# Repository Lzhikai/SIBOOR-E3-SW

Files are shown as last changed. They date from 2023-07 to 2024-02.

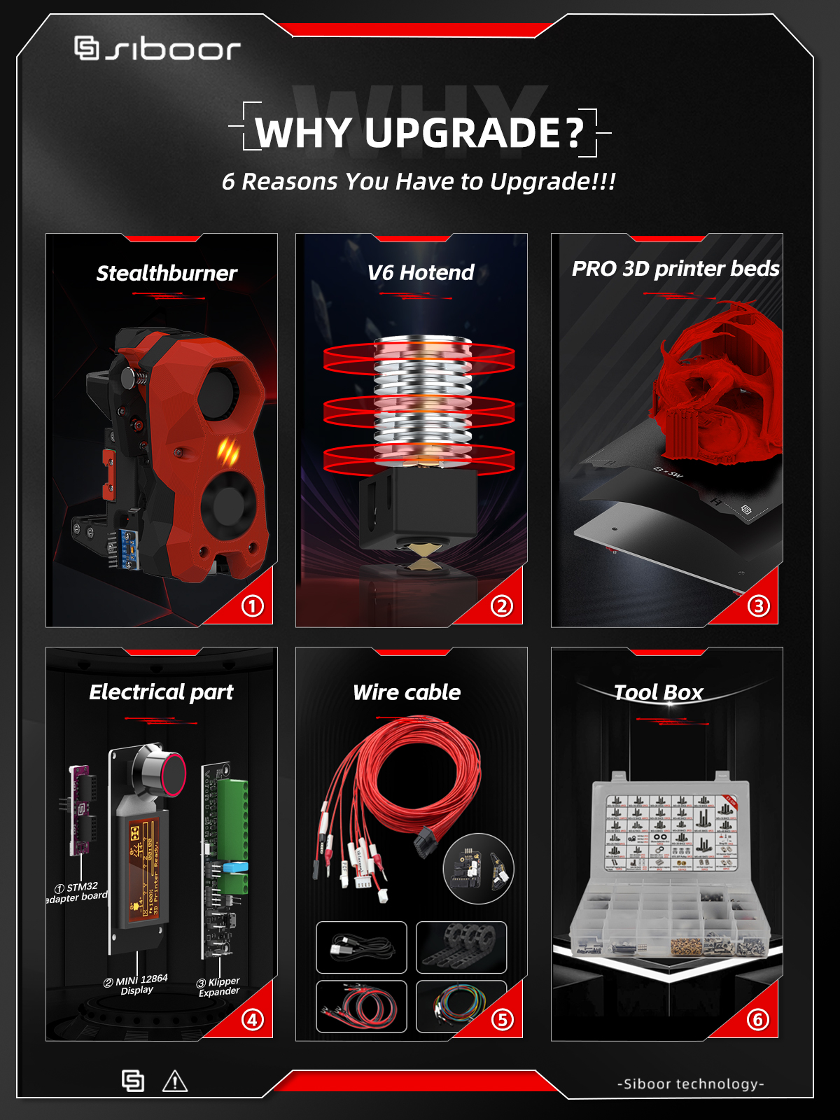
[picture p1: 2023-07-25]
Images/1 (10).jpg

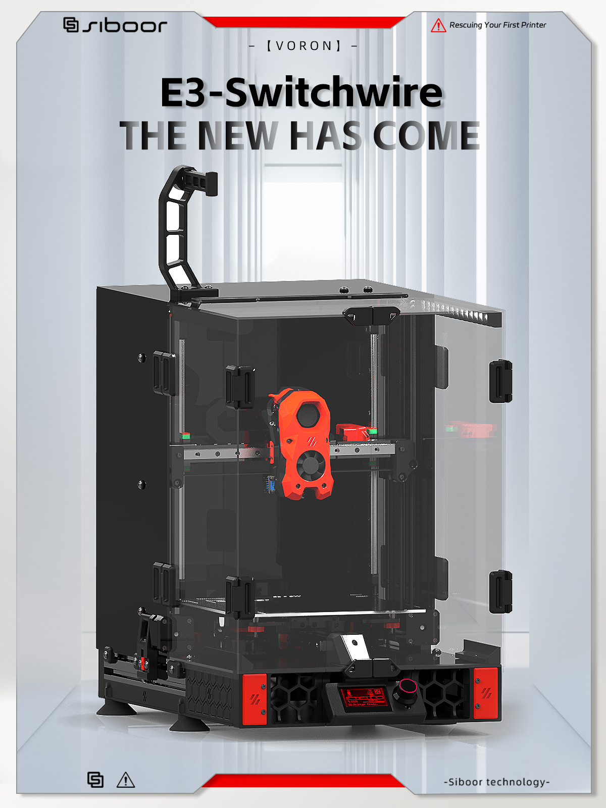
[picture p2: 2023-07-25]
Images/1 (7).jpg

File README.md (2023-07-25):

#SIBOOR E3-SW
We are pleased to announce that we at SIBOOR have launched a conversion kit for E3-SW.
It is based on the open source project DaRk_dOg.

The modifications are as follows
- Use a more cost-effective door closer instead of the KEY-BAK S48K
- Fixed the STL file of Y limit switch
- Used 24→5V step-down module instead of 5V power supply.
- Added klipper extender
- Added STM32 adapter board

Currently the instructions and videos are being made in a hurry, please assemble according to the CAD file, if you encounter problems, you can demand help in discord.

-----------------------------------------------------------------------------------------------------------------------------------------------
Original open source link：https://github.com/boubounokefalos/Ender_SW
architect (of a project)：DaRk_dOg

Original content (citation)

# Ender 3 Pro/V2 to Switchwire Conversion Release.2

This is a full conversion of the popular Ender 3 Pro/V2 to a Voron Switchwire. The motivation came from [Triano](https://github.com/walttriano) and [his awesome original conversion](https://github.com/walttriano/VoronUsers/tree/master/printer_mods/Triano/Ender_3Pro_Switchwire) that served as a starting point, however everything was re-designed from scratch (in order to follow the Voron guidelines and aesthetics more accurately). Another factor that led to this re-design, was the need to be able to enclose this printer in a, visually, pleasant and, structurally, functional way. The ingenious design of 5x MGN12H Linear Rails - 300mm (dual Y axis rail) from Triano was preserved and the printing volume is ~220x220x220.

# Release 2 Update Changelog:

- CAD files cleaned up.
- Small corrections to parts.
- Added printable deck files (still it's recommended to laser cut them though)
- Added different .dxfs for rear black panels (in case anyone wants to cut the panels from a material that is not same on both surfaces)
- Added the option to use the stock Ender 3 LCD screen.

# Rev.2 Update Changelog:

- Every change happened in order to improve the build process and the design overall.
- All screw sizes and types are properly documented in the CAD (soon there will be a conversion BOM also). Also no more “exotic” sizes, everything is according to what VORON is using officially.
- Current conversion’s enclosure is 100% compatible with the new update (except of the deck panels ofc).
- XZ Blocks improved fit for the X v-slots and are also modified to use 30mm BHCS (like the original SW).
- Y Axis, new front idler (in order to achieve a mounting point for the front grill), improved clearance for the rear Y motor mount. All use BHCS screws now.
- Split bed carriage with size and clearance corrections. Made uppon the design recommendation of Steve. Also Y belt clips have a bit more clearance on the upper side, in order to leave some space for spare belt 🙂
- XZ motors have thinner XZ tensioners to avoid the lower “split” (kudos to Steve for that ALSO).
- We are now using the original SW Spool Holder (for easier installation, due to clearance)
- Front Grills have now the LCD mount of the original SW. They also mount to the extended sides just by M3 screws.
- Rear Grills mount by M5x16 BHCS screws now. Also the inlet has moved to the side (in order to have a straight and easier connection with the PSU), this was also a recommendation by Steve and he was more than kind to share his original .F3D file. Both stock Ender and C14 inlets are compatible.
- Removed material from the grills, in order to save some plastic and cut down print time.
- PSU is now mounted parallel to the side extrusions and RS25 can be mounted in the front of the printer.
- Redesigned mounts for the Board and RPi (no more shelf and moooahr clearance!)

And last but not least…
-The side extensions. Front and rear side extensions are designed to extend the frame for aesthetical and a few practical reasons (clearance and NO MORE NOTCH). They are sturdy enough but keep in mind that you will not move around the printer by lifting it from there.

## Info

Various parts _can*_ be recycled from the Ender 3 Pro/V2, most important ones are:
- The frame (though a 310mm extrusion is needed for the X. You can chop the original one to length).
- The MeanWell PSU.
- The heatbed assemble.
- The original board.
- XYZ motors (as long as you can pull off the pulleys. An aftermarket 20mm motor is needed for the printhead extruder though).
- All the cables that don't go through the cable-chains (for there, silicone or PTFE cable is adviced).
- 4010 fan for the tool cooling.

*cheaping out in parts can lead into several problems, such as poor printing quality or, even worse, safety hazard. Keep that in mind and use parts from the official Switchwire BOM.

## Files

- Most of the printed part files needed for this conversion, are included in this git (you will only need to get the Stealthburner print files from the [official Switchwire git](https://github.com/VoronDesign/Voron-Stealthburner) ).
- CAD files (.f3d and .STEP) are provided, in order to help the building process, but they also serve as a BOM (in case you need to find proper screw lengths etc).
- DXF files in order to cut your enclosure panels.
- BOM (Sometime...)

## Credits

- Ofc to Triano, as his design served as base.
- To Steve (THE Steve!) for pointing out weak parts, that had to be redesigned, his tips and files and being a helpful person in general.
- To sdukan#9213 for his valuable help into troubleshooting the Ender 3 V2 differences, electronics (and in general).
- To all of this awesome community of people and especially the [ender_conversion_chat](https://discord.com/channels/460117602945990666/947303252372906014).
- To Voron design team for all the valuable resources and the solid base.

## Disclaimer

This is a very carefuly designed build.. however mistakes could have been made. By deciding to build this conversion, you are responsible for any possible damage done to the printer or even yourself.

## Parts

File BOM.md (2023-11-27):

| style | Name | Quantities | Specs |
|---|---|---|---|
| "Fasteners | M3×8 SHCS | 134 | Black Nickel Plated  |
| | M3×10 SHCS | 4 | Black Nickel Plated  |
| | M3×12 SHCS | 46 | Black Nickel Plated  |
| | M3×16 SHCS | 12 | Black Nickel Plated  |
| | M3×20 SHCS | 10 | Black Nickel Plated  |
| | M3×25 SHCS | 8 | Black Nickel Plated  |
| | M3×30 SHCS | 15 | Black Nickel Plated  |
| | M3×40 SHCS | 15 | Black Nickel Plated  |
| | M3×50 SHCS | 4 | Black Nickel Plated  |
| | M5×40 SHCS | 12 | Black Nickel Plated  |
| | M4×6 SHCS | 2 | Black Nickel Plated  |
| | M4×20 SHCS | 3 | Black Nickel Plated  |
| | M5×10 BHCS | 40 | Black Nickel Plated  |
| | M5×16 BHCS | 35 | Black Nickel Plated  |
| | M5×20 BHCS | 2 | Black Nickel Plated  |
| | M5×25 BHCS | 8 | Black Nickel Plated  |
| | M5×30 BHCS | 10 | Black Nickel Plated  |
| | M5×40 BHCS | 8 | Black Nickel Plated  |
| | M5×25 FHCS | 4 | Black Nickel Plated  |
| | M5 Post-install T-nut | 35 | / |
| | M5 Hammer Head T-nuts | 30 | / |
| | M3 Hammer Head T-nuts | 65 | / |
| | M3 Nut | 6 | Black Nickel Plated  |
| | M4 Nut | 4 | Black Nickel Plated  |
| | M5 Nut | 9 | Black Nickel Plated  |
| | M4×30 FHCS | 4 | Black Nickel Plated  |
| | M3 Brass heatstake inserts - short M3x5x4 | 120 | / |
| | M3Shim 3×7×0.5 | 2 | Black Nickel Plated  |
| | M5 1mm Shim  5×10×1 | 24 | Black Nickel Plated  |
| | M5 rubber gasket 5×10×1 | 12 | / |
| | M2x10 Self Tapping Screws for Plastic | 12 | Black Nickel Plated  |
| | M3×6 FHCS | 24 | Black Nickel Plated  |
| | M3×6 BHCS | 10 | Black Nickel Plated  |
| | M5×45 BHCS | 4 | Black Nickel Plated  |
| | 6mm x 3mm Round Neodymium Magnets | 8 | / |
| | Aluminum column φ5×8×8 | 4 | / |
| "Frame | 2020 Extrusion 310mm long | 1 | / |
| "Electronics  | Nema17 17HS16-2004S1 | 2 | SIBOOR |
| | 24V to 5V DC Voltage Reducer | 1 | / |
| | NEMA14 36mm pancake Motor with 10 tooth gear | 1 | OMC |
| | 5015 blower fans 24V | 1 | SIBOOR |
| | 4010 axial fan 24V | 1 | SIBOOR |
| | 6020 axial fan 24V | 1 | SIBOOR |
| | IEC320 C14 inlet | 1 | / |
| | Stealthburner Neopixel RGBW leds | 1 | SIBOOR |
| | Omron TL-Q5MC2-Z | 1 | OMRON |
| | ADXL345 PCB | 1 | / |
| | ADXL345 lineup | 1 | SIBOOR |
| | V6 hotend | 1 | SIBOOR |
| | 24V 65W Heating（6×15mm Wire length 15cm） | 1 | SIBOOR |
| | NTC 3950 100K（3×15mm Wire length 15cm） | 1 | SIBOOR |
| | klipper expansion board | | FYS |
| | MINI 12864 display | 1 | FYS |
| | STM32 for MINI 12864 Display Converters | 1 | FYS |
| | TYPE-C cable 0.75 meters | 1 | / |
| | Android Data Cable 0.5m | 2 | / |
| | LED strip light 24V white 100mm wire | 1 | / |
| | Micro Switch（15CM） | 1 | SIBOOR |
| Cable Section | Toolhead PCB 14PIN+2PIN Teflon wire | 1 | SIBOOR |
| | raspberry Power supply line | 1 | / |
| | Toolhead PCB（Stealthburner CW2 2PCS） | 1 | SIBOOR |
| | High Flex Wire 20gauge | 2 | / |
| | High Flex Wire 20gauge | 2 | / |
| | Nylon Cable Ties (1.8mm wide or smaller) | 50 | / |
| "Motion | MGN12H 300mm linear guide | 5 | SIBOOR |
| | GT2 20T Pulley (5mm ID 6mm W) | 3 | / |
| | F695 Bearing | 20 | NSK |
| | GT2 Open Belt LL-2GT-6 (6mm wide) - 1500mm | 1 | Gates |
| "Buildplate | 235×235 Black PEI | 1 | / |
| "Panels | Deck left | 1 | / |
| | Deck right | 1 | / |
| | Deck under | 1 | / |
| | Rear Panel | 1 | / |
| | Side Rear panel | 2 | / |
| | Top Rear Panel | 1 | / |
| | Side Clear Panel | 2 | / |
| | Door | 2 | / |
| | Top Clear Panel | 1 | / |
| | Black Door Closer (1KG) | 1 | / |
| "Misc. | Rubber Compressor Foot | 4 | / |
| | 3M 5952 VHB tape 2CM×3M | 1 | 3M |
| | Openable drag chain 10×10 | 3 | / |
| "Extruder | BMG Extruder Kit（With red POM gears） | 1 | SIBOOR |

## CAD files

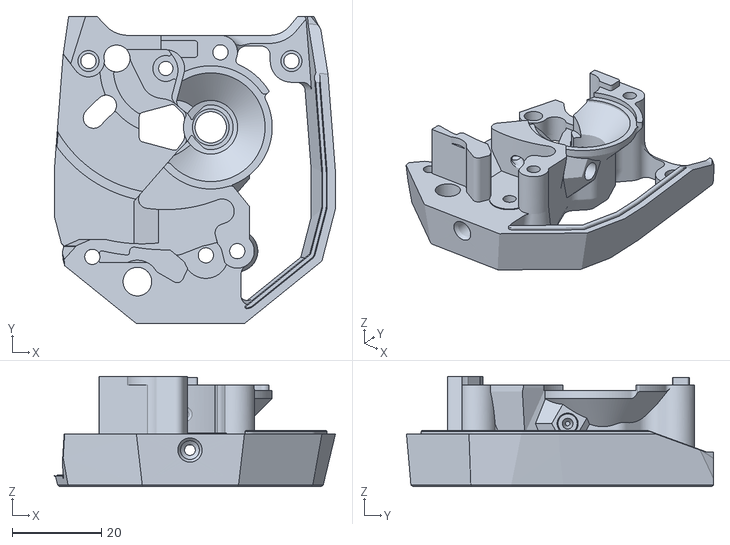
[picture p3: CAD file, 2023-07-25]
STLS - SIBOOR/Hotend/main_body.stl
62.8 x 68.7 x 24.7

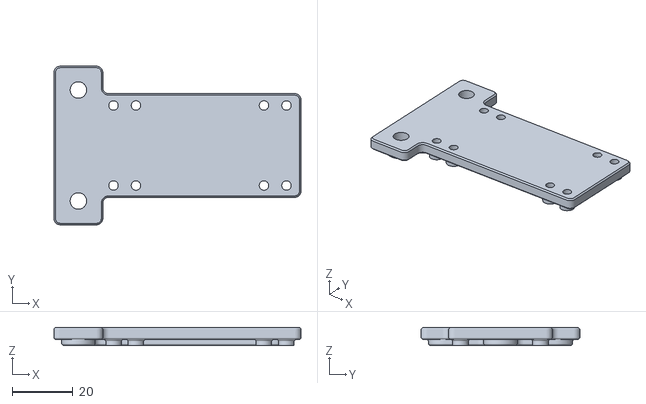
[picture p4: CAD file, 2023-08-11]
STLS - SIBOOR/Electronics/24 Buck 5V module fixing bracket（SIBOOR）.stl
81.0 x 52.0 x 6.00

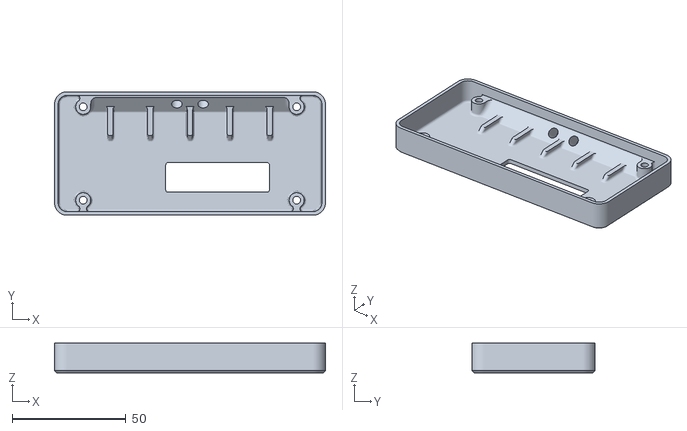
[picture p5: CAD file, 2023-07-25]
STLS - SIBOOR/Electronics/Mini12864/lcd_case_rear_mini12864.stl
119.0 x 54.2 x 13.0

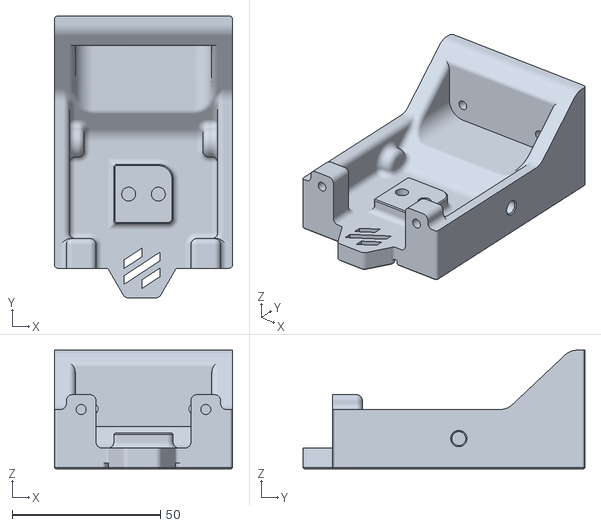
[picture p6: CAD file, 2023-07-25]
STLS - SIBOOR/Extentions/front_extention_left_a.stl
60.0 x 95.0 x 40.0

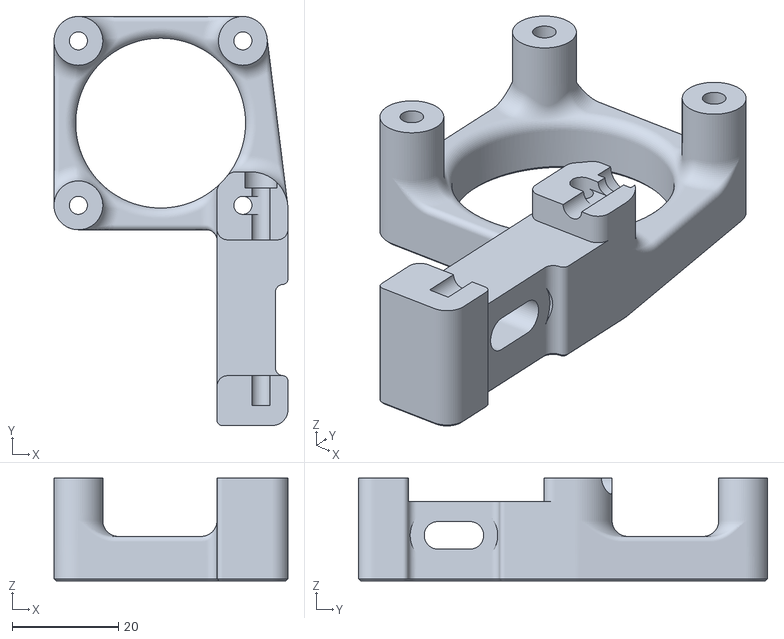
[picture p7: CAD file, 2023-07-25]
STLS - SIBOOR/Gantry/XZ Axis/z_motor_mount_b.stl
44.1 x 77.1 x 19.4

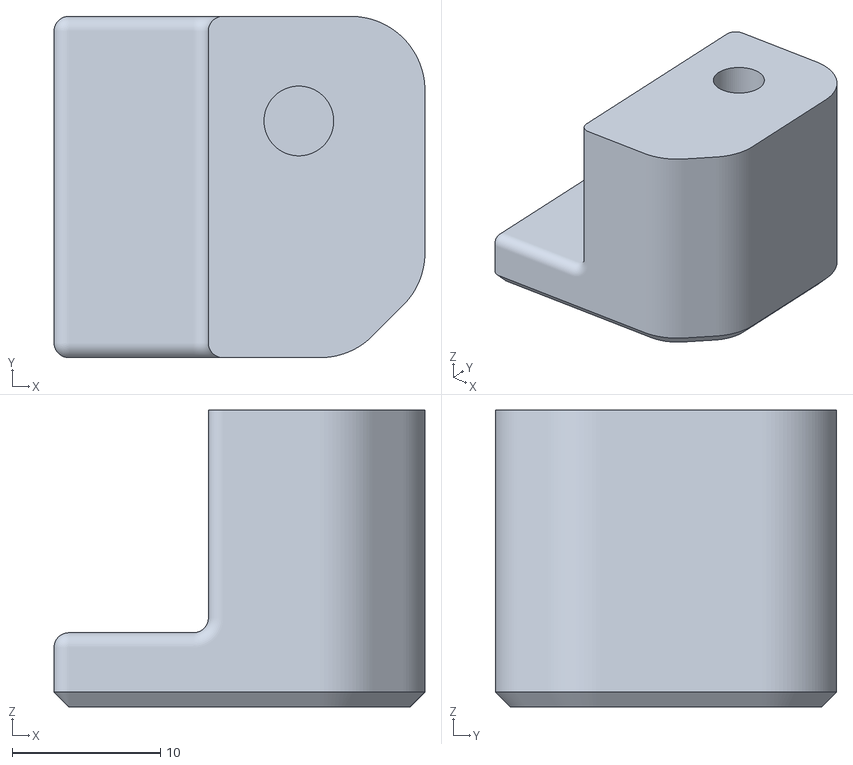
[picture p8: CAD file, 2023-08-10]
STLS - SIBOOR/Grills/grill_rear_left_stock_inlet_shock_blocker.stl
25.0 x 23.0 x 20.0

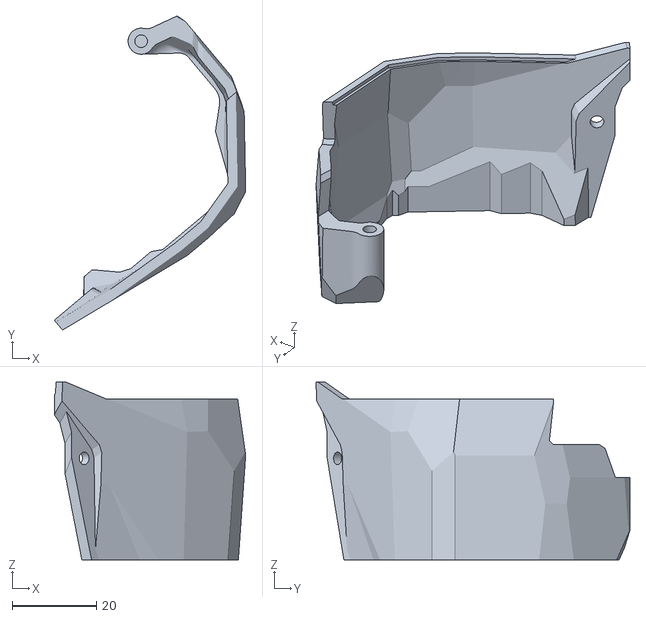
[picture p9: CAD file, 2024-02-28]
STLS - SIBOOR/Hotend/cable_cover_pcb.stl
45.4 x 74.5 x 42.2

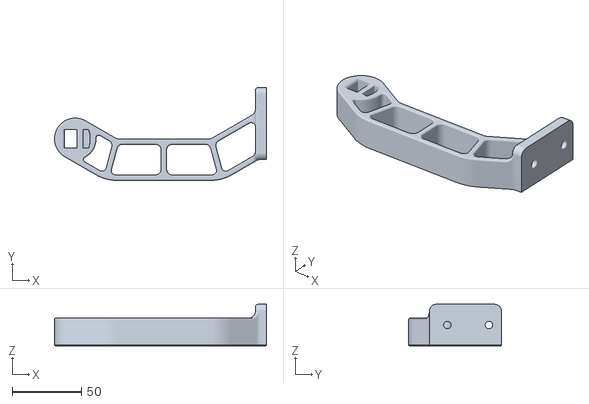
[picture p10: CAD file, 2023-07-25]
STLS - SIBOOR/Misc/spool_holder_base.stl
153.0 x 67.0 x 30.0

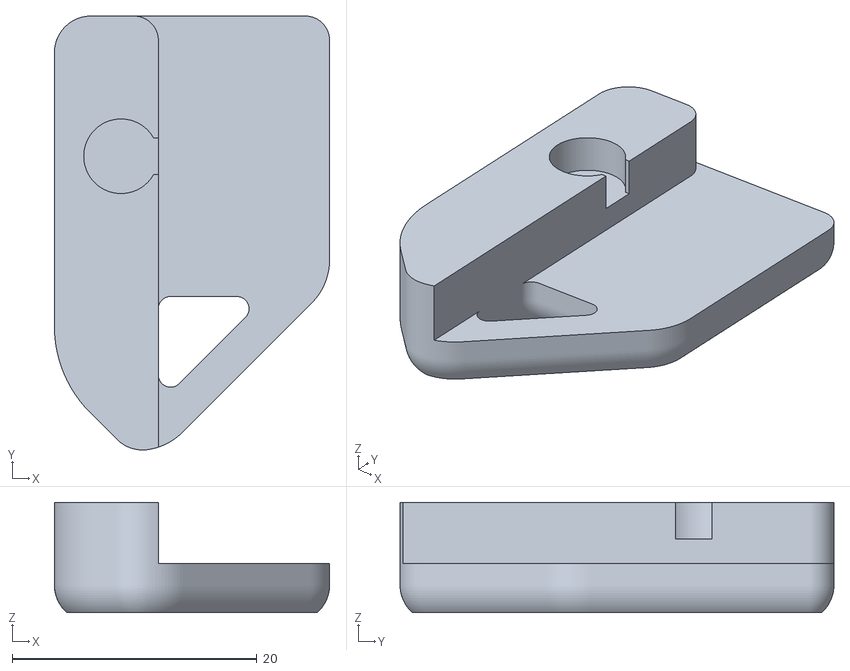
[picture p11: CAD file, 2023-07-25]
STLS - SIBOOR/Panel_Mounting/Doors/door_handle_b_x2.stl
22.5 x 35.5 x 9.00

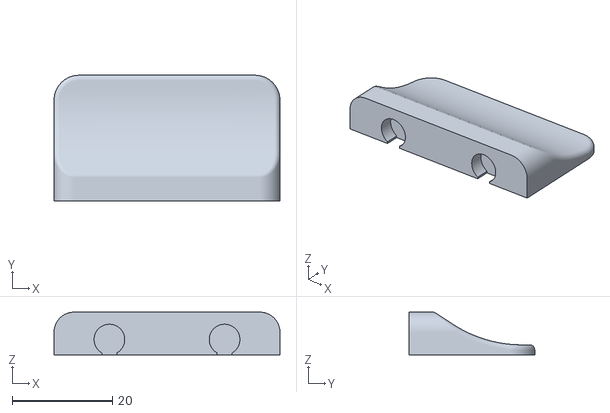
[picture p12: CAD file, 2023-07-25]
STLS - SIBOOR/Panel_Mounting/top_door_latch.stl
45.0 x 25.0 x 8.50

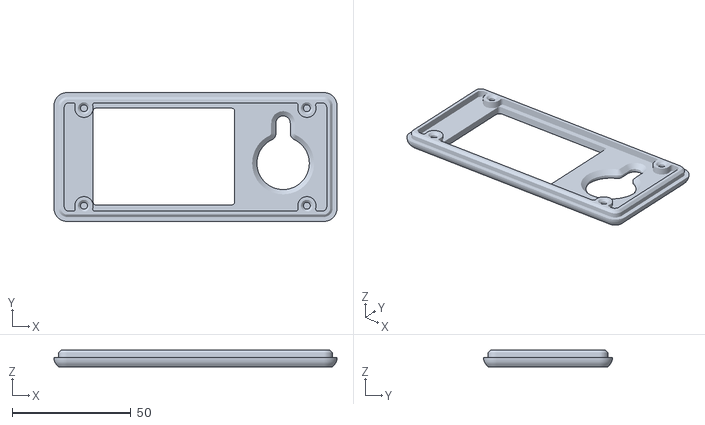
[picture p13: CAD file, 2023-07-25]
STLS - SIBOOR/Electronics/Mini12864/lcd_case_front_mini12864.stl
119.0 x 54.2 x 7.00

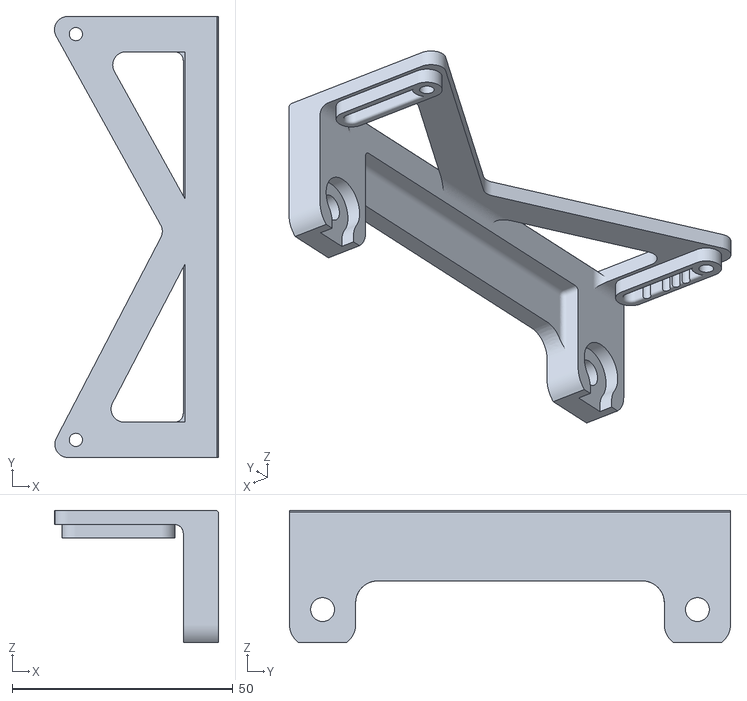
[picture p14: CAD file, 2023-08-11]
STLS - SIBOOR/Electronics/Siboor_EW_Klipper_Expander_Bracket.stl
37.2 x 100.0 x 30.0

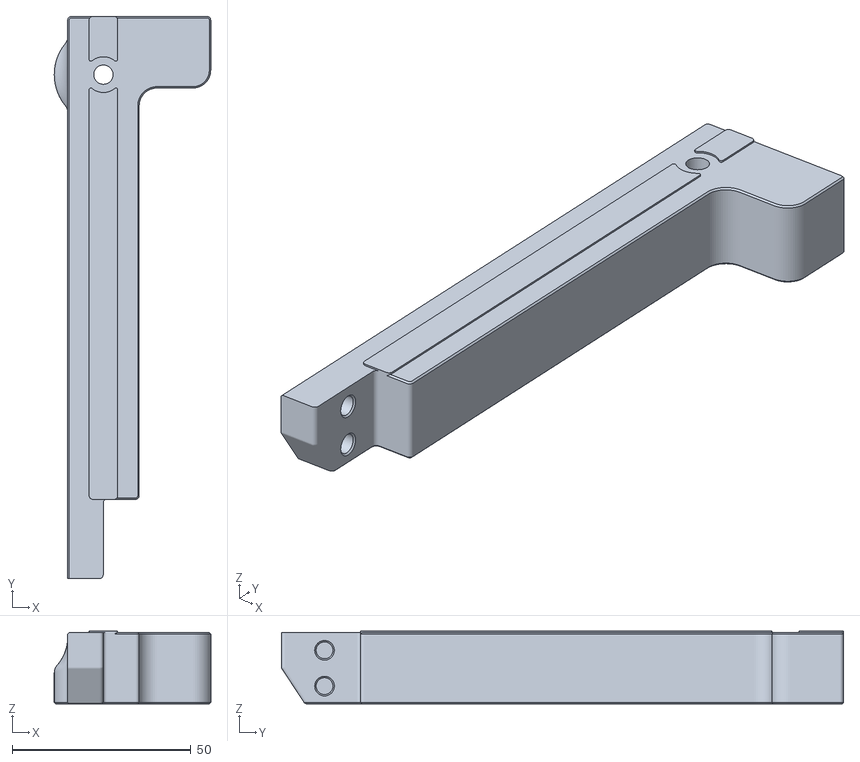
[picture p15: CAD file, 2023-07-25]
STLS - SIBOOR/Extentions/rear_extention_left_b.stl
43.8 x 157.1 x 20.4

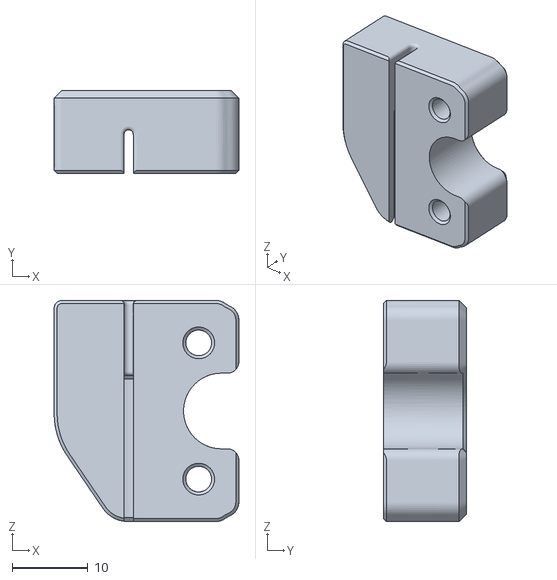
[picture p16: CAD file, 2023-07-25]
STLS - SIBOOR/Gantry/XZ Axis/Door closers gantry anchor（SIBOOR）.stl
24.4 x 11.0 x 29.2

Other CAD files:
STLS - SIBOOR/Gantry/Y Axis/y_idler_a.stl
STLS - SIBOOR/Grills/grill_rear_left_stock_inlet.stl
STLS - SIBOOR/Hotend/[a]_guidler_a.stl
STLS - SIBOOR/Misc/2mm_spacer.stl
STLS - SIBOOR/Electronics/PS_4040_Slide_Mount.stl
STLS - SIBOOR/Electronics/PS_4040_mount_x2.stl
STLS - SIBOOR/Electronics/RPi_bracket.stl
STLS - SIBOOR/Electronics/skr_mini_e3_mount.stl
STLS - SIBOOR/Extentions/front_extention_left_b.stl
STLS - SIBOOR/Extentions/front_extention_right_a.stl
STLS - SIBOOR/Extentions/front_extention_right_b.stl
STLS - SIBOOR/Extentions/rear_extention_left_a.stl
STLS - SIBOOR/Extentions/rear_extention_right_a.stl
STLS - SIBOOR/Extentions/rear_extention_right_b.stl
STLS - SIBOOR/Extentions/support_arm_x2.stl
STLS - SIBOOR/Gantry/XZ Axis/Door closer holder（SIBOOR）.stl
STLS - SIBOOR/Gantry/XZ Axis/[a]_upper_idler_support_b_left.stl
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

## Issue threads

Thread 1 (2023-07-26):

Missing GPL license

thetic, 2023-07-26:
This is derivative work of https://github.com/boubounokefalos/Ender_SW and https://github.com/VoronDesign/Voron-Switchwire so it needs to retain the GPL license.

thetic, 2023-07-26:
Resolved in 57890187f16171f497db78470454dd5498b0e177. Thank you!

Closed 2023-07-26.

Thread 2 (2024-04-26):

Sample printer.cfg for a Creality 4.2.2 board?

rquackenbush, 2024-04-26:
I'm building a Siboor Enderwire kit and was hoping to get a printer.cfg for my setup. My setup:
- Creality 4.2.2
- Klipper Expansion board
- STM32 for MINI 12864 Display Converters

Do you have a sample printer.cfg for this configuration?

Fonsecal, 2025-02-19:
Same question , any Printer.cfg for this mount ??

Mumie1980, 2025-03-13:
Need the Printer.cfg for this Ender3 V2 3D printer upgrade kit Voron E3-Switchwire Stealthburner for my setup the same as from rquackenbush?

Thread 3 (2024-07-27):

BOM is missing M3x30 SCHS

YoungHillionaire, 2024-07-27:
Manual calls for 4 M3x30 SCHS for X motor mount and 4 M3x30 SCHS
And 8 for the z blocks
Yet the kit comes with only 15 screws

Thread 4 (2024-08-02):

Front extension screws are wrong in manual

YoungHillionaire, 2024-08-02:
Multiple manual errors
Front Extensions manual calls for M3x8 but too short
So i checked the CAD files showing M3x12

Computerchic, 2025-02-15:
Acabo de darme cuenta de eso. Muchas gracias. Espero que se pongan las pilas y corrijan el error en el manual.  Gracias

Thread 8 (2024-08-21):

Incorrect stealthburner chain anchor stl

FrostiFish, 2024-08-21:
The repo includes the regular chain anchor. This part has incorrect dimensions for the Switchwire. The chain_anchor_2hole_sw.stl should be used instead. It provides a little extra clearance near the max limit for the Z-axis. It also has correct alignment with the mounting slot on the x-axis extrusion.

Best regards,
Hannah

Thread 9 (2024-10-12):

[a]_latch.stl is outdated

FrostiFish, 2024-10-12:
The latch broke on my printer. I compared the STLs of this repository and the Stealthburner repository. The one in the stealthburner repository has been updated and reinforced, so it won't break as easily. I would highly recommend to update this stl file
